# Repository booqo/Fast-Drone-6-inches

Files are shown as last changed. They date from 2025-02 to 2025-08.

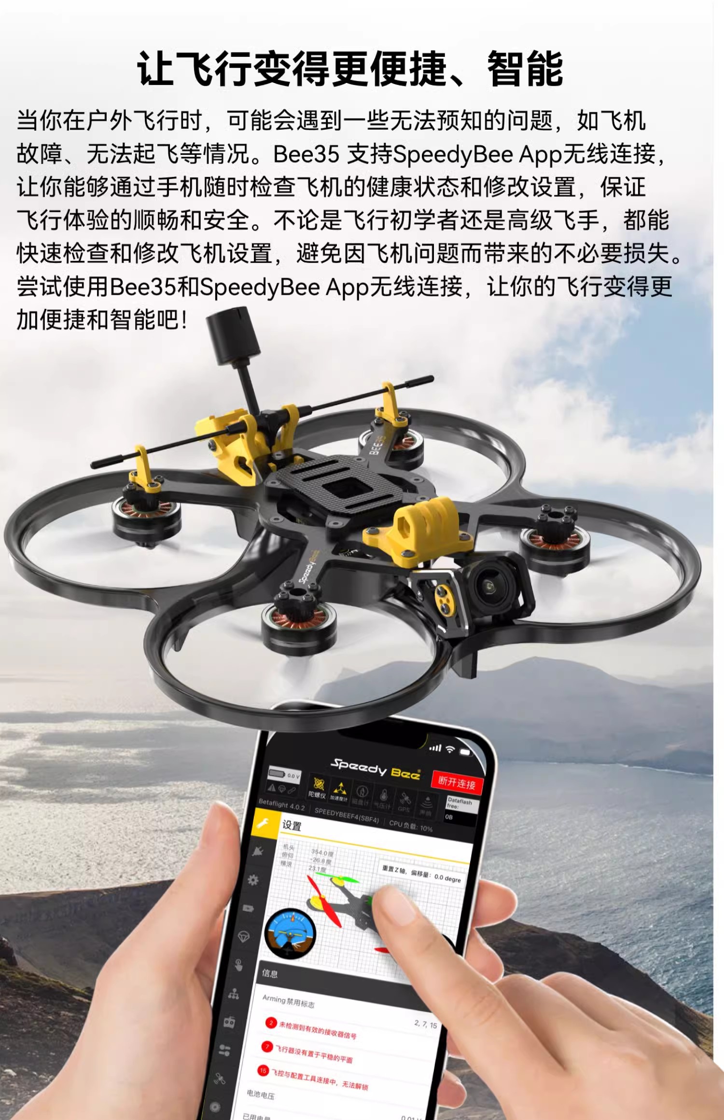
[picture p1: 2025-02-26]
CAD/reference/各种飞机图片用于参考/O1CN01pKsIaQ1XnORmsjtUH_!!721822968.jpg

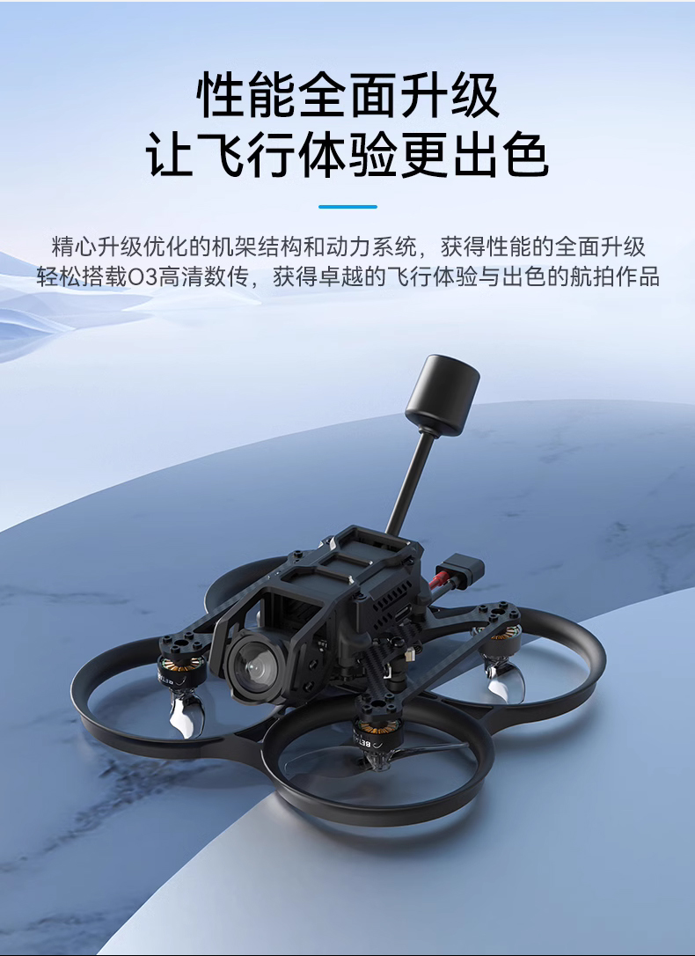
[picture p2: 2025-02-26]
CAD/reference/各种飞机图片用于参考/O1CN01ygFc3O1XnOTsRyGer_!!721822968.jpg

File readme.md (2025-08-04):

<font size=6> **从零制作自主空中机器人** </font>

本文档是视频教程[从零制作自主空中机器人](https://www.bilibili.com/video/BV1WZ4y167me?p=1)的配套文档,github链接为https://github.com/ZJU-FAST-Lab/Fast-Drone-250

<font color="#dd0000">安全事项</font>

四旋翼无人机具有较高的安全风险，请同学们严格遵守安全规范，不要在有人的室内或室外进行试验，对自己和他人的安全负责，本实验室完全免责

- [第一章：课程介绍](#第一章课程介绍)
- [第二章：动力套焊接](#第二章动力套焊接)
- [第三章：飞控的安装与接线](#第三章飞控的安装与接线)
- [第四章：飞控设置与试飞](#第四章飞控设置与试飞)
- [第五章：机载电脑与传感器的安装](#第五章机载电脑与传感器的安装)
- [第六章：Ubuntu20.04的安装](#第六章ubuntu2004的安装)
- [第七章：机载电脑的环境配置](#第七章机载电脑的环境配置)
- [第八章：常用实验与调试软件的安装与使用](#第八章常用实验与调试软件的安装与使用)
- [第九章：Ego-Planner代码框架与参数介绍](#第九章ego-planner代码框架与参数介绍)
- [第十章：VINS的参数设置与外参标定](#第十章vins的参数设置与外参标定)
- [第十一章：Ego-Planner的实验](#第十一章ego-planner的实验)
- [Q&A 常见问题及解答](#qa-常见问题及解答)

## 第一章：课程介绍
  本次课程是一套面向对自主空中机器人感兴趣的学生、爱好者、相关从业人员的免费课程，包含了从硬件组装、机载电脑环境设置、代码部署、实机实验等全套详细流程，带你从0开始，组装属于自己的自主无人机，并让它可以在未知的环境中自由避障穿行。本次课程所涉及的所有代码、硬件设计全部开源，<font color="#dd0000">严禁商用与转载，版权与最终解释权由浙江大学FASTLAB实验室所有。</font>
  本次课程的重心主要落在自主空中机器人的搭建、代码部署及调试上，关于自主空中机器人的一些理论基础，例如动力学模型，路径搜索，轨迹规划，地图构建等内容，高飞老师在深蓝学院有非常详尽而深入浅出的[课程](https://www.shenlanxueyuan.com/course/385?source=1)，本次课程就不再赘述。

## 第二章：动力套焊接
  机器人本体相关配件及焊接用工具详见[purchase_list.xlsx](purchase_list.xlsx),对硬件选型有相关疑问请看 番外一：硬件选型
## 第三章：飞控的安装与接线
* 一定要注意电调信号线顺序！！！
  电机方向
* 飞控箭头与机头同向为正向，任意方向旋转90°的倍数也可以，后续可以在飞控设置内调整，推荐和视频内相同朝向摆放。
* <font color="#dd0000">强烈推荐使用硅胶杜邦线，常规杜邦线线材过硬，容易出现接触不良。</font>
* 5V稳压模块注意贴黑胶带绝缘，周围注意贴一圈厚的海绵胶带来防止飞机降落时损坏5V模块，也可以考虑把5V模块用扎带扎在机臂旁边
* 使用V5+飞控或其他把模拟和数字输出分开的飞控（特点是输出口标号为A1~A4 M1~M4），如果要用Dshot协议，请插在A口上

## 第四章：飞控设置与试飞

* 请烧录本git项目下的`/firmware/px4_fmu-v5_default.px4`固件，这个固件是官方1.11.0版本固件编译而来，如有需要可以自行编译。实测1.13版本固件存在BUG，不建议使用，更老的固件版本未经测试。

* 在飞控的sd卡的根目录下创建`/etc/extras.txt`，写入

  ```
  mavlink stream -d /dev/ttyACM0 -s ATTITUDE_QUATERNION -r 200
  mavlink stream -d /dev/ttyACM0 -s HIGHRES_IMU -r 200
  ```
  
  以提高imu发布频率
  
* 修改机架类型为 `Generic 250 Racer`，代指250mm轴距机型。如果是其他尺寸的机架，请根据实际轴距选择机架类型

* 修改`dshot_config`为dshot600

* 修改`CBRK_SUPPLY_CHK`为894281 *执行这步跳过了电源检查，因此左侧栏的电池设置部分就算是红的也没关系*

* 修改`CBRK_USB_CHK`为197848

* 修改`CBRK_IO_SAFETY`为22027

* 修改`SER_TEL1_BAUD`为921600

* 修改`SYS_USE_IO`为0（搜索不到则不用管）

* 上电前请先用万用表通断档检测电源正负焊点是否短接，强烈建议第一次上电前先接一个[短路保护器](https://item.taobao.com/item.htm?spm=a230r.1.14.6.72b83b20uNbZk7&id=656973651729&ns=1&abbucket=19#detail)

* <font color="#dd0000">检测电机转向前确保没有安装螺旋桨！！！！</font>

* 修改电机转向：进入mavlink控制台

  ```
  dshot reverse -m 1
  dshot save -m 1
  ```

  修改`1`为需要反向的电机序号
  
* <font color="#dd0000">第一次试飞请务必找有自稳模式下飞行经验的飞手协助，只飞过大疆无人机的飞手99%无法飞好！</font>

* 身边没有有经验的飞手怎么办？详见Q&A

## 第五章：机载电脑与传感器的安装

* 碳板已经预留了拆壳NUC的安装空位。如果想拆壳安装NUC，需要额外购买USB网卡，或者拆下自带的网卡天线找地方固定住，并且由于碳纤维板导电，请务必用尼龙柱把NUC支起来，相关资料请自行查阅。
* 机载电脑使用4S航模电池直接供电，正常情况下没有问题。但理论上最好接一个稳压模块，否则在无人机炸机/电池几乎耗尽时会出现机载电脑关机的情况。但由于符合NUC功率的稳压模块比较大，请同学们酌情选用。

## 第六章：Ubuntu20.04的安装

* 镜像站地址：`http://mirrors.aliyun.com/ubuntu-releases/20.04/` 下载 `ubuntu-20.04.4-desktop-amd64.iso`
* 烧录软件UltraISO官网：`https://cn.ultraiso.net/`
* 分区设置：
  * EFI系统分区（主分区）512M
  * 交换空间（逻辑分区）16000M（内存大小的两倍）
  * 挂载点`/`（主分区）剩余所有容量
  * <font color="#dd0000">笔记本上也需要安装ubuntu，推荐装20.04版本。虚拟机或双系统都可以，如果有长期学习打算推荐双系统</font>
## 第七章：机载电脑的环境配置

* ROS安装
  * `sudo sh -c 'echo "deb http://packages.ros.org/ros/ubuntu $(lsb_release -sc) main" > /etc/apt/sources.list.d/ros-latest.list'`
  * `sudo apt-key adv --keyserver 'hkp://keyserver.ubuntu.com:80' --recv-key C1CF6E31E6BADE8868B172B4F42ED6FBAB17C654`
  * `sudo apt update`
  * `sudo apt install ros-noetic-desktop-full`
  * `echo "source /opt/ros/noetic/setup.bash" >> ~/.bashrc`
  * <font color="#dd0000">建议没有ROS基础的同学先去B站学习古月老师的ROS入门教程</font>
* 测试ROS
  * 打开三个终端，分别输入
  * `roscore`
  * `rosrun turtlesim turtlesim_node`
  * `rosrun turtlesim turtle_teleop_key`
* realsense驱动安装
  * `sudo apt-key adv --keyserver keyserver.ubuntu.com --recv-key  F6E65AC044F831AC80A06380C8B3A55A6F3EFCDE || sudo apt-key adv --keyserver hkp://keyserver.ubuntu.com:80 --recv-key  F6E65AC044F831AC80A06380C8B3A55A6F3EFCDE`
  * `sudo add-apt-repository "deb https://librealsense.intel.com/Debian/apt-repo $(lsb_release -cs) main" -u`
  * `sudo apt-get install librealsense2-dkms`
  * `sudo apt-get install librealsense2-utils`
  * `sudo apt-get install librealsense2-dev`
  * `sudo apt-get install librealsense2-dbg`
  * 测试：`realsense-viewer`
  * <font color="#dd0000">注意测试时左上角显示的USB必须是3.x，如果是2.x，可能是USB线是2.0的，或者插在了2.0的USB口上（3.0的线和口都是蓝色的）</font>
* 安装mavros
  * `sudo apt-get install ros-noetic-mavros`
  * `cd /opt/ros/noetic/lib/mavros`
  * `sudo ./install_geographiclib_datasets.sh`
* 安装ceres与glog与ddyanmic-reconfigure
  * 解压`3rd_party.zip`压缩包
  * 进入glog文件夹打开终端
  * `./autogen.sh && ./configure && make && sudo make install`
  * `sudo apt-get install liblapack-dev libsuitesparse-dev libcxsparse3.1.2 libgflags-dev libgoogle-glog-dev libgtest-dev`libcxsparse3.1.2版本可能不匹配？改成libcxsparse3就可以
  * 进入ceres文件夹打开终端
  * `mkdir build`
  * `cd build`
  * `cmake ..`
  * `sudo make -j4`
  * `sudo make install`
  * `sudo apt-get install ros-noetic-ddynamic-reconfigure`
* 下载ego-planner源码并编译
  * `git clone https://github.com/ZJU-FAST-Lab/Fast-Drone-250`
  * `cd Fast-Drone-250`
  * `catkin_make`
  * `source devel/setup.bash`
  * `roslaunch ego_planner single_run_in_sim.launch`
  * 在Rviz内按下键盘G键，再单击鼠标左键以点选无人机目标点

## 第八章：常用实验与调试软件的安装与使用

* VScode：`sudo dpkg -i ***.deb`
* Terminator：`sudo apt install terminator`
* Plotjuggler：
  * `sudo apt install ros-noetic-plotjuggler`
  * `sudo apt install ros-noetic-plotjuggler-ros`
  * `rosrun plotjuggler plotjuggler`
* Net-tools：
  * `sudo apt install net-tools`
  * `ifconfig`
* ssh：
  * `sudo apt install openssh-server`
  * 在笔记本上：`ping 192.168.**.**`
  * `sudo gedit /etc/hosts`
  * 加上一行：`192.168.**.** fast-drone`
  * `ping fast-drone`
  * `ssh fast-drone@fast-drone`(`ssh 用户名@别名`)

## 第九章：Ego-Planner代码框架与参数介绍
* `src/planner/plan_manage/launch/single_run_in_exp.launch`下的：
  * `map_size`：当你的地图大小较大时需要修改，注意目标点不要超过map_size/2
  * `fx/fy/cx/cy`：修改为你的深度相机的实际内参（下一课有讲怎么看）
  * `max_vel/max_acc`：修改以调整最大速度、加速度。速度建议先用0.5试飞，最大不要超过2.5，加速度不要超过6
  * `flight_type`：1代表rviz选点模式，2代表waypoints跟踪模式
* `src/planner/plan_manage/launch/advanced_param_exp.xml`下的：
  * `resolution`：代表栅格地图格点的分辨率，单位为米。越小则地图越精细，但越占内存。最小不要低于0.1
  * `obstacles_inflation`：代表障碍物膨胀大小，单位为米。建议至少设置为飞机半径（包括螺旋桨、桨保）的1.5倍以上，但不要超过`resolution`的4倍。如果飞机轴距较大，请相应改大`resolution`
* `src/realflight_modules/px4ctrl/config/ctrl_param_fpv.yaml`下的：
  * `mass`：修改为无人机的实际重量
  * `hover_percent`：修改为无人机的悬停油门，可以通过px4log查看，具体可以参考[文档](https://www.bookstack.cn/read/px4-user-guide/zh-log-flight_review.md) 如果你的无人机是和课程的一模一样的话，这项保持为0.3即可。如果更改了动力配置，或重量发生变化，或轴距发生变化，都请调整此项，否则自动起飞时会发生无法起飞或者超调严重的情况。
  * `gain/Kp,Kv`：即PID中的PI项，一般不用太大改动。如果发生超调，请适当调小。如果无人机响应较慢，请适当调大。
  * `rc_reverse`：这项使用乐迪AT9S的不用管。如果在第十一课的自动起飞中，发现飞机的飞行方向与摇杆方向相反，说明需要修改此项，把相反的通道对应的值改为true。其中throttle如果反了，实际实验中会比较危险，建议在起飞前就确认好，步骤为：
    * `roslaunch mavros px4.launch`
    * `rostopic echo /mavros/rc/in`
    * 打开遥控器，把遥控器油门从最低满满打到最高
    * 看echo出来的消息里哪项在缓慢变化（这项就是油门通道值），并观察它是不是由小变大
    * 如果是由小变大，则不需要修改throttle的rc_reverse，反之改为true
    * 其他通道同理
  
## 第十章：VINS的参数设置与外参标定
* 检查飞控mavros连接正常
  * `ls /dev/tty*`，确认飞控的串口连接正常。一般是`/dev/ttyACM0`
  * `sudo chmod 777 /dev/ttyACM0`，为串口附加权限
  * `roslaunch mavros px4.launch`
  * `rostopic hz /mavros/imu/data_raw`，确认飞控传输的imu频率在200hz左右
* 检查realsense驱动正常
  * `roslaunch realsense2_camera rs_camera.launch`
  * 进入远程桌面，`rqt_image_view`
  * 查看`/camera/infra1/image_rect_raw`,`/camera/infra2/image_rect_raw`,`/camera/depth/image_rect_raw`话题正常
* VINS参数设置
  * 进入`realflight_modules/VINS_Fusion/config/`
  
  * 驱动realsense后，`rostopic echo /camera/infra1/camera_info`，把其中的K矩阵中的fx,fy,cx,cy填入`left.yaml`和`right.yaml`
  
  * 在home目录创建`vins_output`文件夹(如果你的用户名不是fast-drone，需要修改config内的vins_out_path为你实际创建的文件夹的绝对路径)
  
  * 修改`fast-drone-250.yaml`的`body_T_cam0`和`body_T_cam1`的`data`矩阵的第四列为你的无人机上的相机相对于飞控的实际外参，单位为米，顺序为x/y/z，第四项是1，不用改
  
* VINS外参精确自标定
  * `sh shfiles/rspx4.sh`
  * `rostopic echo /vins_fusion/imu_propagate`
  * 拿起飞机沿着场地<font color="#dd0000">尽量缓慢</font>地行走，场地内光照变化不要太大，灯光不要太暗，<font color="#dd0000">不要使用会频闪的光源</font>，尽量多放些杂物来增加VINS用于匹配的特征点
  * 把`vins_output/extrinsic_parameter.txt`里的内容替换到`fast-drone-250.yaml`的`body_T_cam0`和`body_T_cam1`
  * 重复上述操作直到走几圈后VINS的里程计数据偏差收敛到满意值（一般在0.3米内）
* 建图模块验证
  * `sh shfiles/rspx4.sh`
  * `roslaunch ego_planner single_run_in_exp.launch`
  * 进入远程桌面 `roslaunch ego_planner rviz.launch`

## 第十一章：Ego-Planner的实验
* 自动起飞：

  * `sh shfiles/rspx4.sh`
  * `rostopic echo /vins_fusion/imu_propagate`
  * 拿起飞机进行缓慢的小范围晃动，放回原地后确认没有太大误差
  * 遥控器5通道拨到内侧，六通道拨到下侧，油门打到中位
  * `roslaunch px4ctrl run_ctrl.launch`
  * `sh shfiles/takeoff.sh`，如果飞机螺旋桨开始旋转，但无法起飞，说明`hover_percent`参数过小；如果飞机有明显飞过1米高，再下降的样子，说明`hover_percent`参数过大
  * 遥控器此时可以以类似大疆飞机的操作逻辑对无人机进行位置控制
  * 降落时把油门打到最低，等无人机降到地上后，把5通道拨到中间，左手杆打到左下角上锁
* Ego-Planner实验
  * 自动起飞
  * `roslaunch ego_planner single_run_in_exp.launch`
  * `sh shfiles/record.sh`
  * 进入远程桌面 `roslaunch ego_planner rviz.launch`
  * 按下G键加鼠标左键点选目标点使无人机飞行
* <font color="#dd0000">如果实验中遇到意外怎么办！！！</font>
  * `case 1`: VINS定位没有飘，但是规划不及时/建图不准确导致无人机规划出一条可能撞进障碍物的轨迹。如果飞手在飞机飞行过程中发现无人机可能会撞到障碍物，在撞上前把6通道拨回上侧，此时无人机会退出轨迹跟随模式，进入VINS悬停模式，在此时把无人机安全着陆即可
  * `case 2`：VINS定位飘了，表现为飞机大幅度颤抖/明显没有沿着正常轨迹走/快速上升/快速下降等等，此时拨6通道已经无济于事，必须把5通道拨回中位，使无人机完全退出程序控制，回到遥控器的stablized模式来操控降落
  * `case 3`：无人机已经撞到障碍物，并且还没掉到地上。此时先拨6通道，看看飞机能不能稳住，稳不住就拨5通道手动降落
  * `case 4`：无人机撞到障碍物并且炸到地上了：拨5通道立刻上锁，减少财产损失
  * `case 5`：**绝招** 反应不过来哪种case，或者飞机冲着非常危险的区域飞了，直接拨7通道紧急停桨。这样飞机会直接失去动力摔下来，对飞机机身破坏比较大，一般慢速情况下不建议。

## Q&A 常见问题及解答

	Q: 能不能用265+435来不跑vins？
	A: 可以，但265直出的里程计的速度估计有问题，可能导致控制不稳定。需要把265和imu做ekf融合。
	
	Q: 硬件清单中的xxx能不能更换？
	A: 请看视频番外一，讲解了大部分替换可能。
	   如果要换大轴距机架，请相应更换动力套及桨叶。pid参数也需要相应调整，相关内容自行查阅。
	   435相机可以换430相机。430更便宜但没有外壳，不好固定且容易炸坏。
	   电池不建议更换，因为课程的Q250机架刚刚好可以塞入2300mah 4S电池，不需要额外固定。更换电池需要自行解决电池放置问题。
	
	Q: 能不能用D435i自带的imu运行vins?
	A: 不行，因为435的imu噪声很大
	
	Q: 课程提供的v1.11.0固件有什么改动吗？必须使用这个固件吗？
	A: 没有任何改动，是直接从px4官方下载的。目前仅在该版本上测试通过了本套代码，且在v1.13上测试失败，表现为VINS会经常崩溃。其他飞控/其他版本固件没有测试，有需要的同学可以自行测试。
	
	Q: QGC内测试电机不转怎么办？
	A: 1. 检查电调是否支持dshot，不支持请自行查阅pwm电调校准方法。 
	   2.如果是使用V5+飞控或其他把模拟和数字输出分开的飞控（特点是输出口标号为A1~A4 M1~M4），如果要用Dshot协议，请插在A口上
	   3.使用holybro pixhawk4完全版飞控，飞控与分电板的插线请插在FMU PWM OUTPUT上，而非I/O PWM OUTPUT
	
	Q: 运行vins后报红字错误？
	A: 大概率是你改config后格式错误，照着报错去修改对应的config
	
	Q: 运行vins后报"VINS_RESULT_PATH not opened"?
	A: 在home目录创建`vins_output`文件夹(如果你的用户名不是fast-drone，需要修改config内的vins_out_path为你实际创建的文件夹的绝对路径)
	
	Q: 这台飞机的载重有多少？续航有多少？能飞多远？
	A: 不带额外负载起飞重量在1.1~1.2kg左右，最大起飞重量在1.8kg内，再大控制不稳且续航很短。
		不带负载续航约5分钟。
		能飞多远取决于你wifi的通讯质量，一般wifi顶多通讯100米。此外由于栅格地图直接开在内存内，如果地图范围设置过大，容易占满内存导致其他程序运行缓慢。一般不建议超过50米*50米。
		
	Q: 为什么要挡住D435的结构光？
	A: 结构光的意义在于使相机得到的深度图更准确，但双目图片上会显示出位置固定不变的点阵光斑，这对VIO的运行是不利的，所以需要关掉。
	
	Q: VINS飘怎么办？
	A: 1. 检查环境中是否有强反光物体（瓷砖、玻璃等）
	   2. 尽量缓慢地移动无人机，场景内不要有运动物体
	   3. 尽量准确地测量初始外参
	   4. 不要在运行vins的时候在远程桌面上运行rviz（会占用大量CPU资源），实在想开建议去配一下ROS多机，然后在笔记本上开
	   5. 检查环境中是否有频闪光源（肉眼无法看出，在realsense的单目画面中检查）
	
	Q: 我没有自稳模式无人机的飞行经验，身边也没有有经验的飞手，怎么办呢？
	A: 1. 有预算的情况下，建议购买一台耐摔的带保护圈的穿越机来练手，推荐的型号有mobula6,吉朗小金鱼85x,化骨龙racewhoop30等
	   2. 没啥预算的情况下，建议购买一个遥控器加密狗来把课程推荐的AT9S遥控器连接到电脑，然后在模拟器里练熟。模拟器推荐steam上的liftoff,免费的推荐free rider
	
	Q: 我想用NX做机载电脑，该另外做些什么？
	A: 原则上不建议小白用NX，会多很多麻烦事，本课程并不涉及，助教也没有时间去帮你看。
	   需要额外做下面的事：
	   1. 修改VINS为GPU版本的，因为NX的CPU算力很差，跑课程的CPU版VINS一定跑不动
	   2. 解决NX固定及供电问题
	   3. 解决realsense固定问题
	   4. 解决NX用小底板时接口不够的问题
	   5. 解决一系列arm和x86不兼容带来的问题
	   
	Q: 我按照教程修改sd卡里的etc/extra.txt后，IMU频率没有变成200hz怎么办？
	A: 可能原因是你的固件不支持这样修改，可以尝试在启动mavros后执行：
	rosrun mavros mavcmd long 511 105 5000 0 0 0 0 0 & sleep 1;
	rosrun mavros mavcmd long 511 31 5000 0 0 0 0 0 & sleep 1;

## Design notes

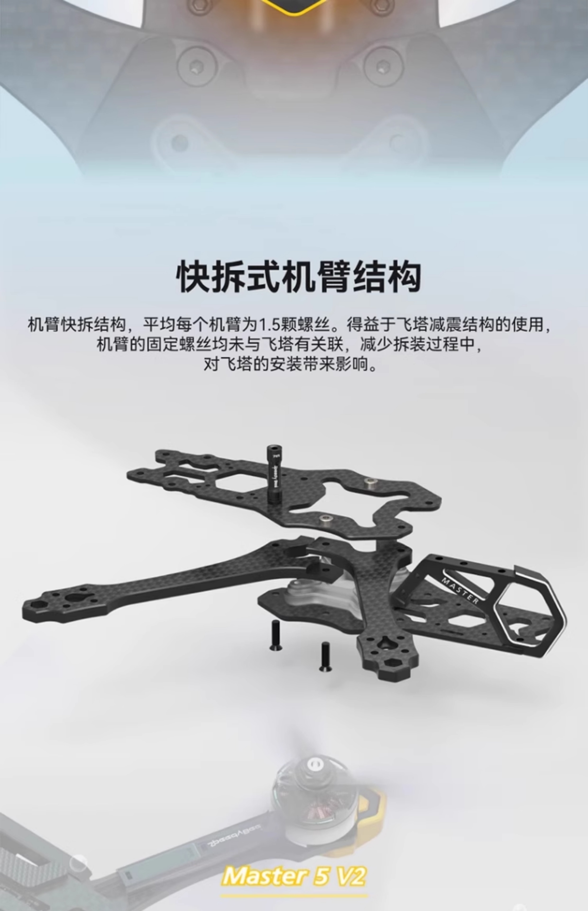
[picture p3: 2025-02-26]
CAD/reference/各种飞机图片用于参考/O1CN01WyYj862ADSTkLBOoo_!!290188169.jpg

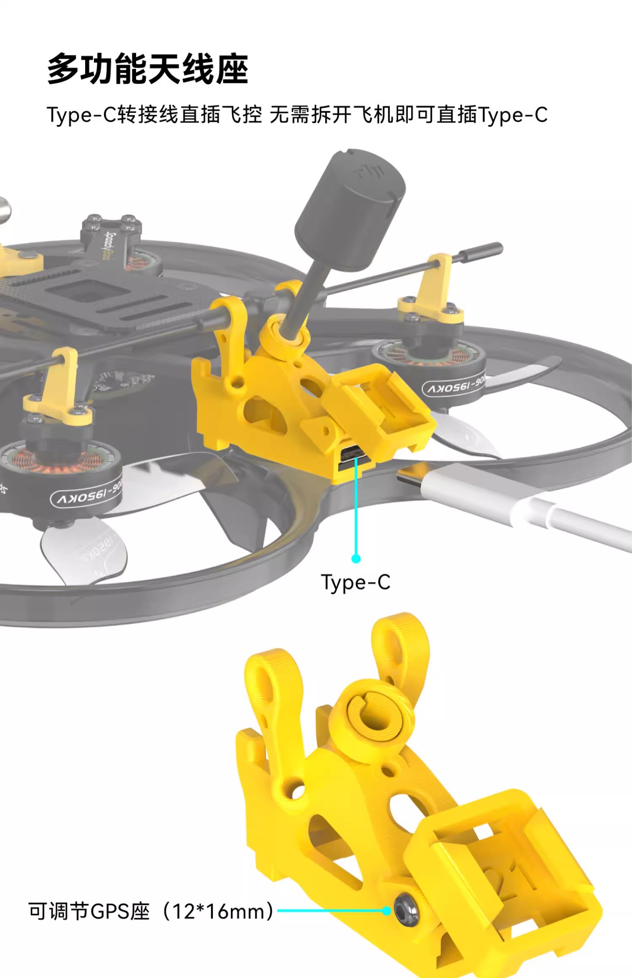
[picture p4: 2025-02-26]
CAD/reference/各种飞机图片用于参考/O1CN016cnDkM1XnORoAMxxN_!!721822968.jpg

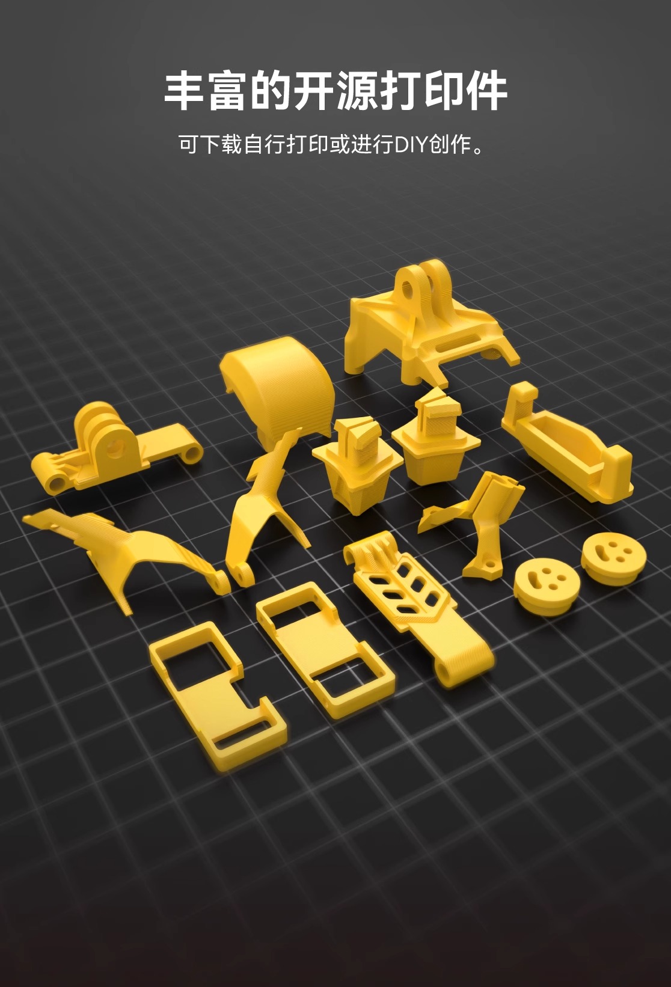
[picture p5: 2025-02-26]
CAD/reference/各种飞机图片用于参考/O1CN01xL4YBd1MtNuao2uYQ_!!2206811492.jpg

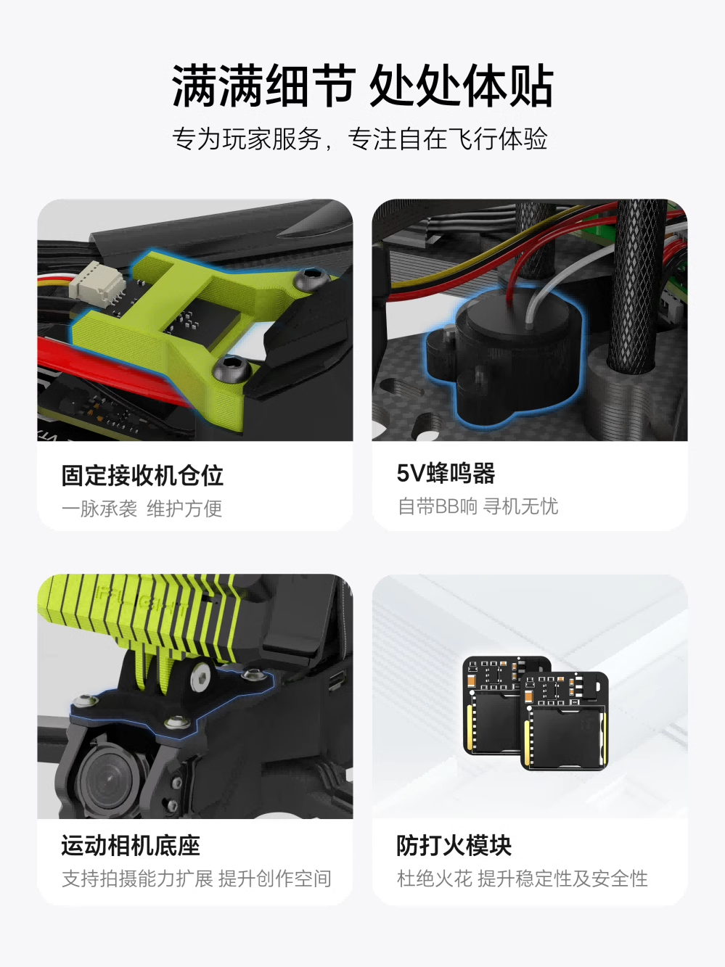
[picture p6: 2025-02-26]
CAD/reference/各种飞机图片用于参考/O1CN01gszA4X1mHzbSsJmLc_!!830904930.png

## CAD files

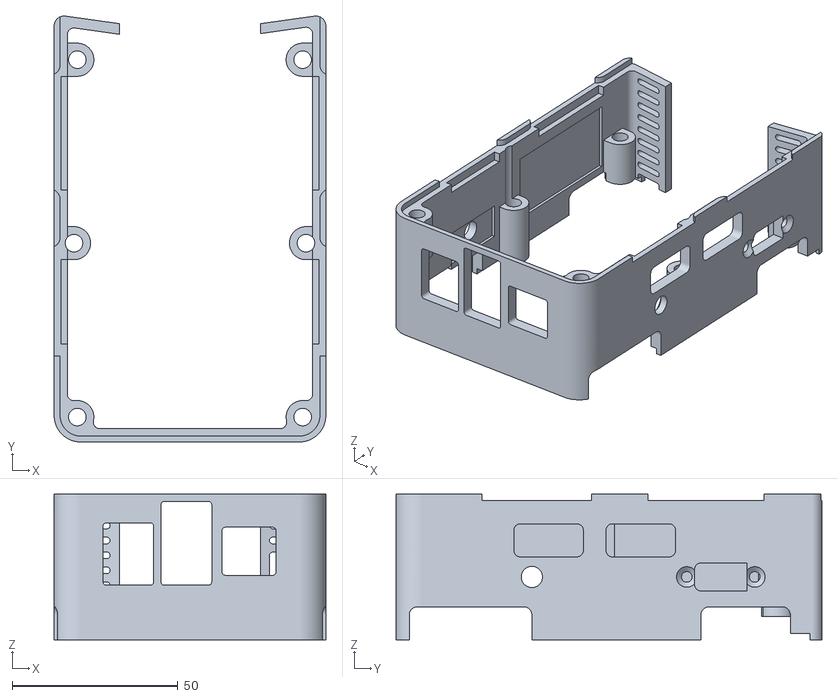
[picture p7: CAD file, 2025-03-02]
CAD/3d_print_test/555.stl
82.0 x 128.5 x 44.0

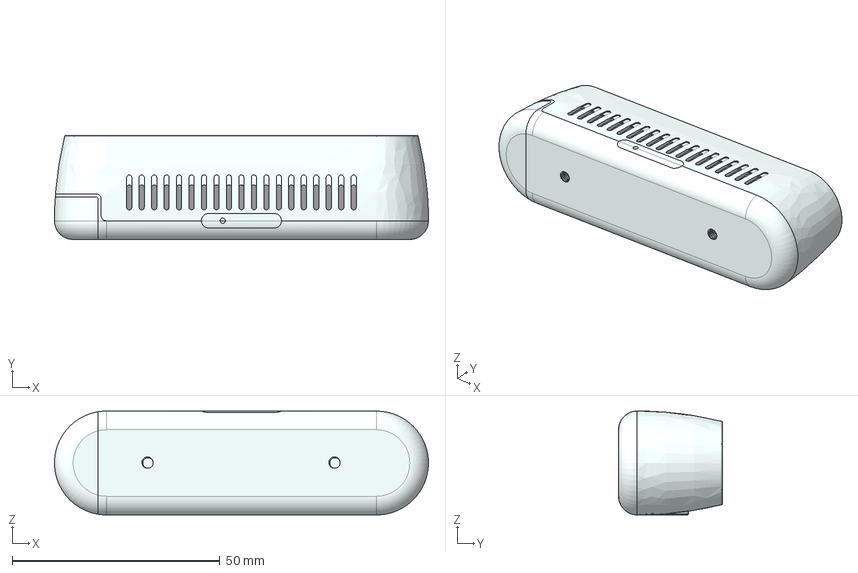
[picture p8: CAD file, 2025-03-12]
CAD/camera/intel-realsense-d435-3d-camera-1.snapshot.6/Intel Realsense D435.stp
90.0 x 25.0 x 25.0 mm

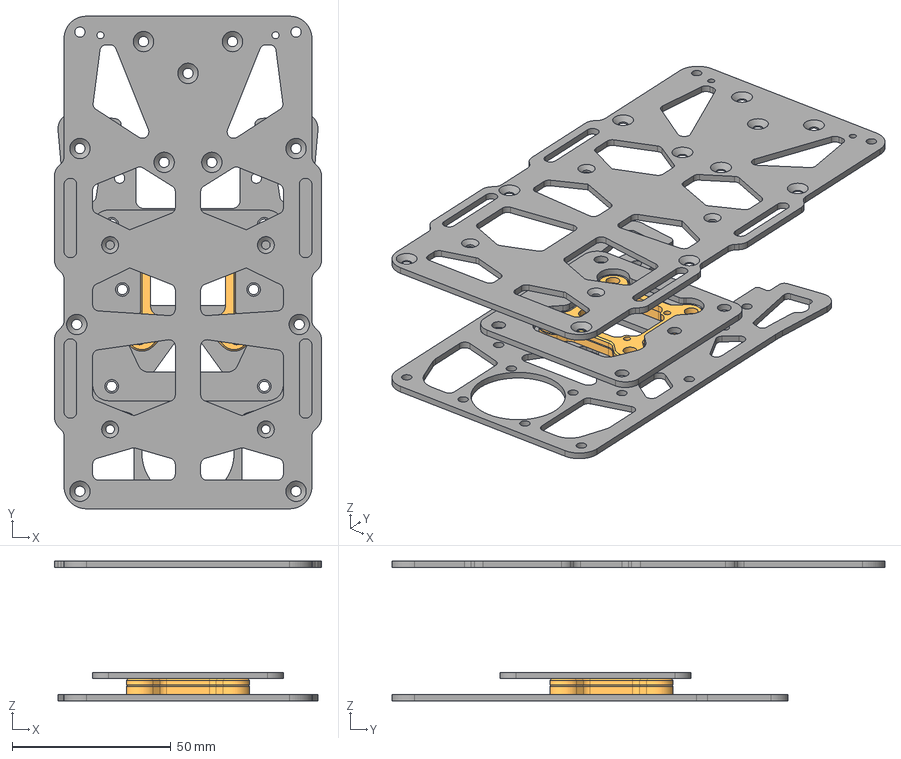
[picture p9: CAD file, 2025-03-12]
CAD/jiagong/CENTER_RACK_other.stp
84.0 x 155.0 x 44.0 mm

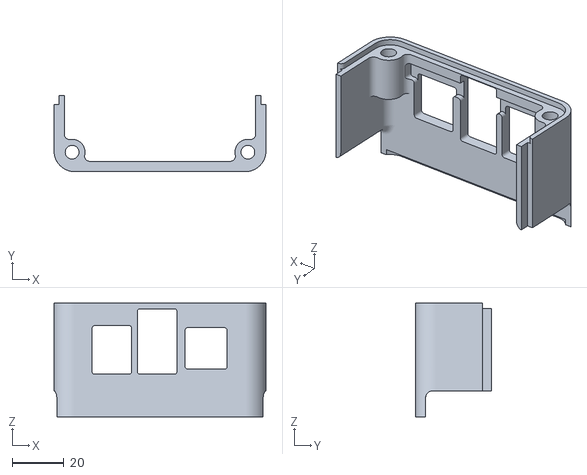
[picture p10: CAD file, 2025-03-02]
CAD/3d_print_test/88.stl
82.0 x 29.5 x 44.0

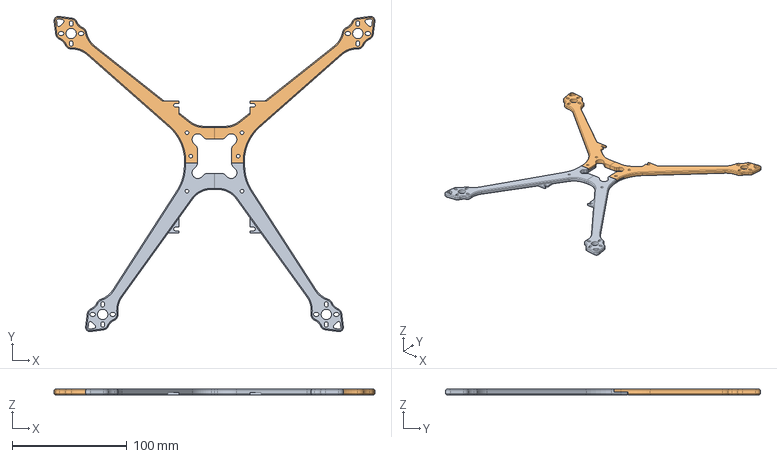
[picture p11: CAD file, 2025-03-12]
CAD/jiagong/center_rack.stp
279.9 x 274.9 x 5.00 mm

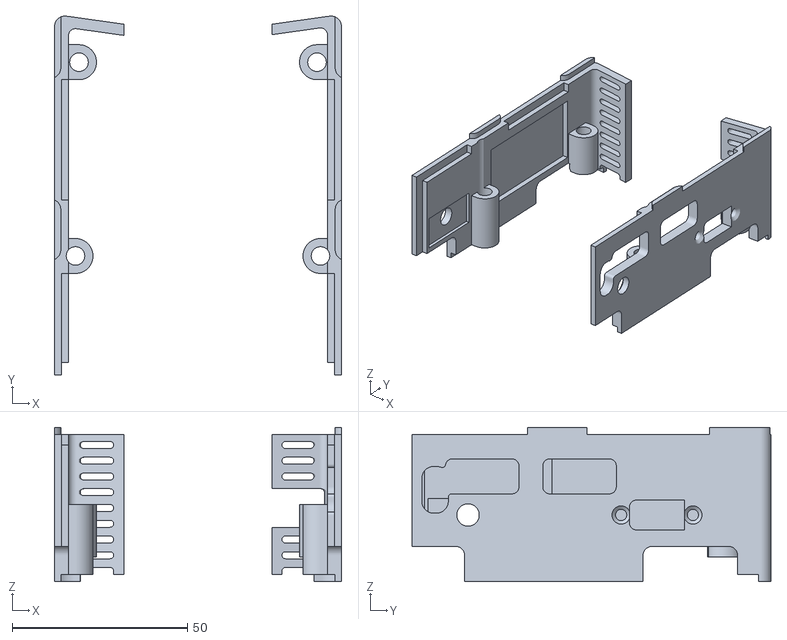
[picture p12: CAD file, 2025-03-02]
CAD/3d_print_test/999.stl
82.0 x 102.5 x 44.0

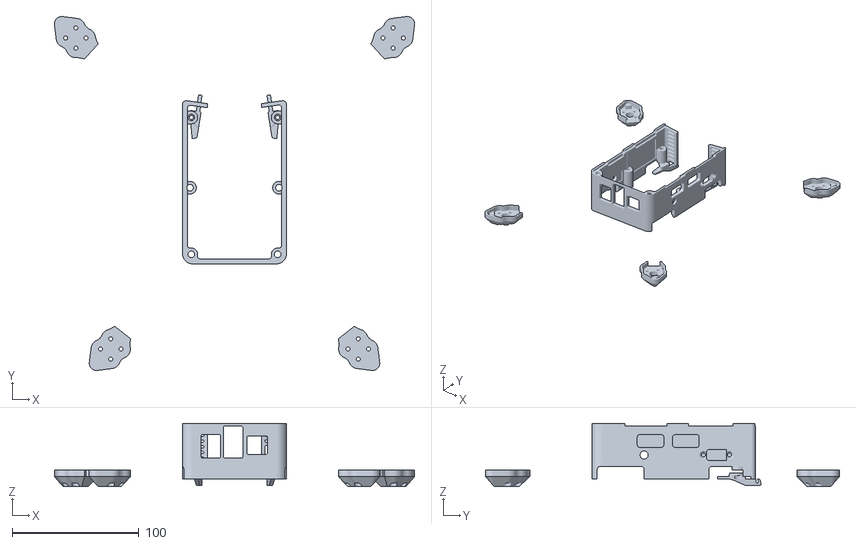
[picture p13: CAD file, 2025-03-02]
CAD/3d_print_test/444.stl
283.9 x 278.9 x 50.0

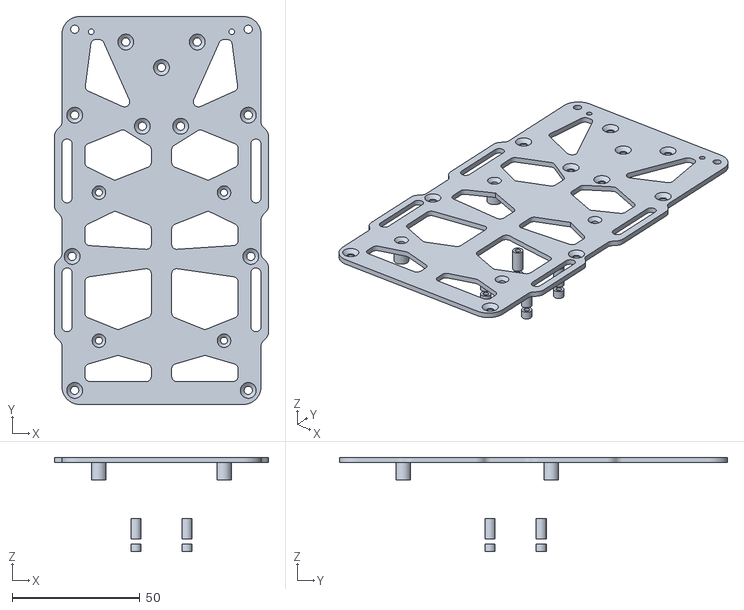
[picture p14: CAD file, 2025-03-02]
CAD/3d_print_test/888.stl
84.0 x 152.0 x 37.0

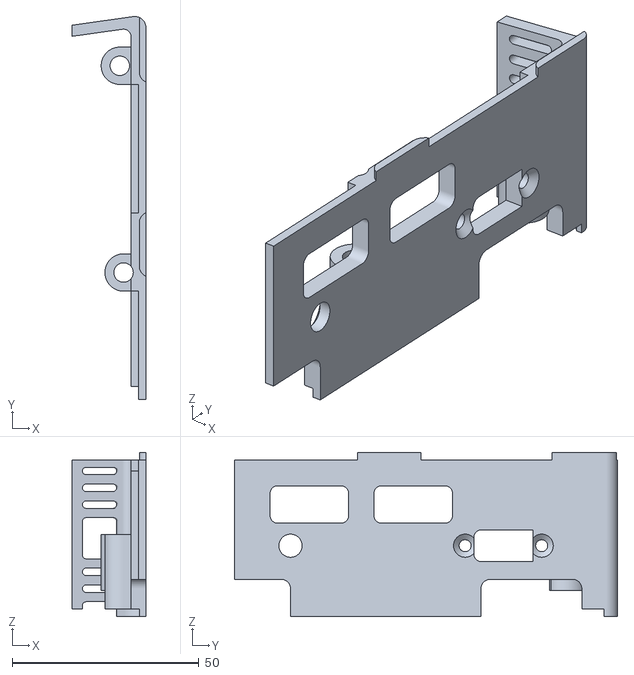
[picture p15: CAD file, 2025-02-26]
CAD/3d_print_test/333.stl
19.8 x 102.5 x 44.0

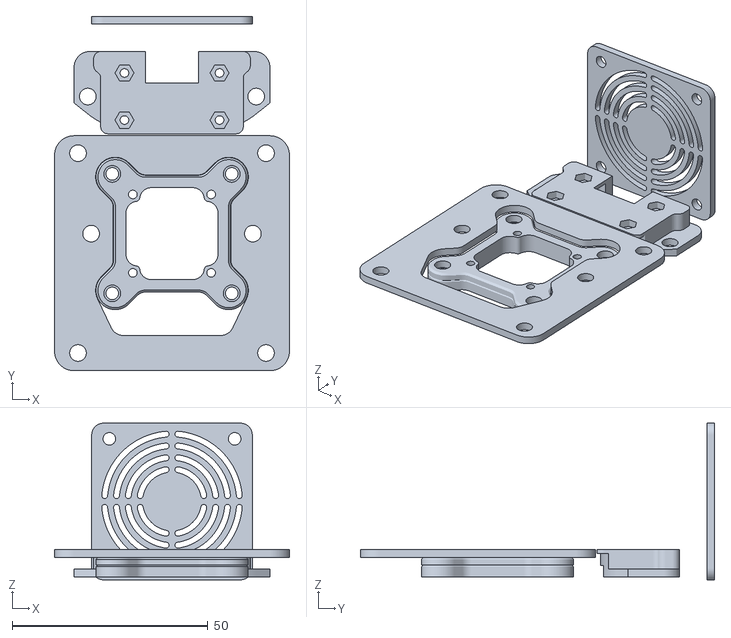
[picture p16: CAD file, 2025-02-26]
CAD/3d_print_test/222.stl
60.0 x 90.5 x 40.0

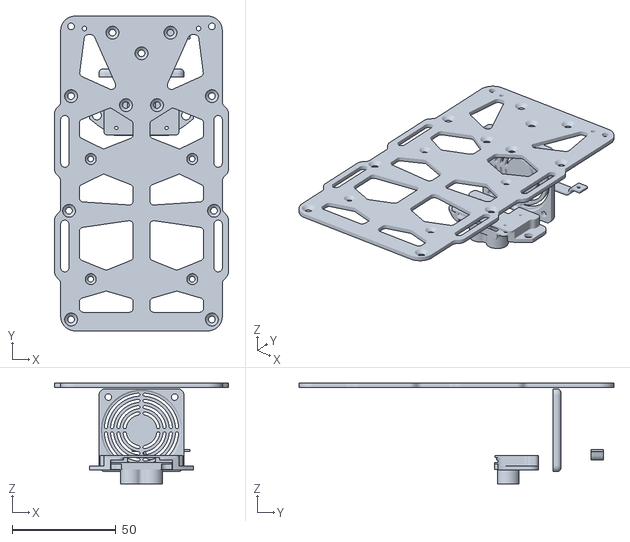
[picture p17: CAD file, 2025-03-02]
CAD/3d_print_test/111111.stl
84.0 x 152.0 x 48.7

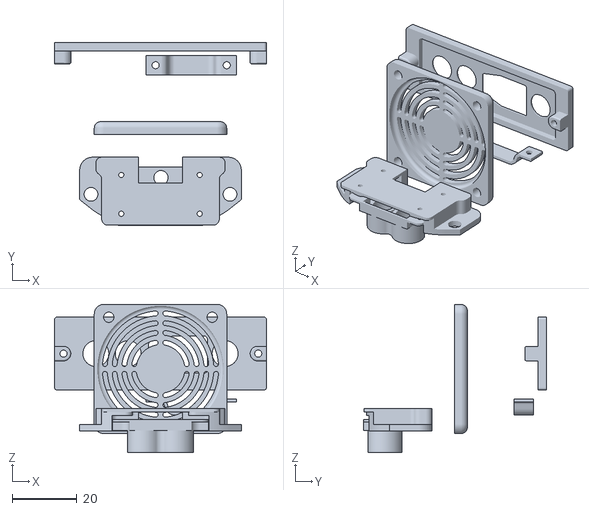
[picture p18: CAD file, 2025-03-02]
CAD/3d_print_test/101010.stl
65.6 x 56.5 x 45.9

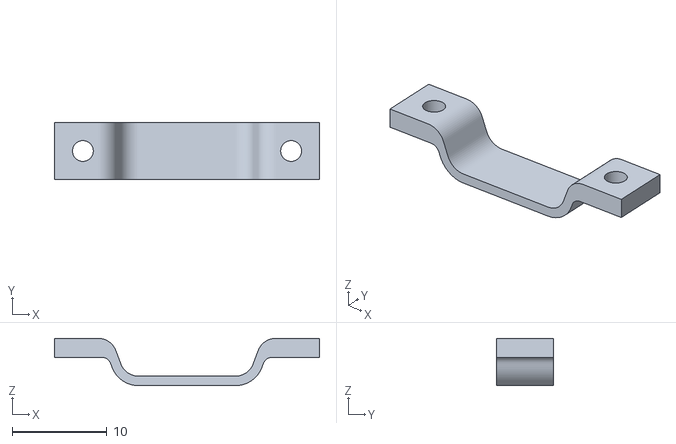
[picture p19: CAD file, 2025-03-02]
CAD/3d_print_test/121212.stl
28.0 x 6.00 x 5.00

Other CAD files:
CAD/3d_print_test/666.stl
CAD/3d_print_test/777.stl
CAD/3010fan.prt
CAD/40x40x7 DC Fan.prt
CAD/5VBec.prt
CAD/CENTER_RACK.prt
CAD/CLA_M3_2.prt
CAD/GPS_RACK.prt
CAD/M3X35.prt
CAD/M3X38.prt
CAD/M3X40.prt
CAD/MOTOR_TEMP.prt
CAD/TypecRack.prt
CAD/back.prt
CAD/battery.prt
CAD/battery/battery_1.prt
CAD/battery/battery_2.prt
CAD/battery/battery_3.prt
CAD/battery/battery_4.prt
CAD/battery/battery_5.prt
CAD/battery/battery_6.prt
CAD/bottom.prt
CAD/bottom_rack.prt
CAD/camear_hat.prt
CAD/camera/D435.prt
CAD/camera/D435_rack.prt
CAD/camera/camera_srew.prt
CAD/camera/intel-realsense-d435-3d-camera-1.snapshot.6/Intel Realsense D435.SLDPRT
CAD/camera_rack.prt
CAD/esc_rack.prt
CAD/fan_rack.prt
CAD/flow_rack.prt
CAD/foot_rack.prt
CAD/foot_rack2.prt
CAD/foot_rack3.prt
CAD/foot_rack4.prt
CAD/foot_rack5.prt
CAD/foot_stool.prt
CAD/jianzheng.prt
CAD/jianzheng2.prt
CAD/left_side.prt
CAD/lvM3_10x10.prt
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

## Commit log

2025-02-26 add CAD
    [222.stl, 3010fan.prt, 333.stl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]
2025-03-02 updata cad modle
    [101010.stl, 111111.stl, 121212.stl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]
2025-03-12 update cad
    [CENTER_RACK.prt, CENTER_RACK_other.stp, D435.prt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]
2025-03-15 updata battery6
    [battery_6.prt]
2025-03-17 updata cad
    [CENTER_RACK.prt, D435_rack.prt, battery.prt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]
2025-03-18 add D435 rack
    [CENTER_RACK.prt, D435_rack.prt, GPS_RACK.prt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]
2025-03-20 Updata camera rack
    [CENTER_RACK.prt, D435_rack.prt]
